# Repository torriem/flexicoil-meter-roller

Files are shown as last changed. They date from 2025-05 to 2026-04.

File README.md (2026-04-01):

A collection of CAD files pertaining to the Flexicoil 50 series and older air cart meter rollers.  An OpenSCAD library, called "Flexicoil Meter Segment.scad" creates various kinds of meter roller segments, for 3-D printing.  Currently implemented roller types are extra fine (canola), fine (wheat), coarse (fertlizer, peas), extra coarse (large peas etc), and blank, with a 1 1/8" hex hole through them.  Dimensions defining the diameter and width of the rollers, as well as printer tolerances for the hex hole, are in dimensions.scad.

dimensions.scad defines common dimensions used by all the meter roller segment types and Flexicoil Meter Segment.scad contains parametric segment creator modules.

`Extra Fine Segments.scad`, `Fine Segments.scad`, `Coarse Segments.scad`, and `Extra Coarse Segments.scad` demonstrate all of the variants of the different segment types possible.  In order to create an STL of a specific variant, comment out the other module calls in the scad file before exporting to STL.

Most objects can be printed without supports.  The bearing endcap can be printed as it renders (with the open cup up) with supports in TPU 95A, with between 25 and 50% infill.  Supports, even when made with TPU, seem to remove pretty well.  

Meter segments seem to print quite well with TPU 95A, with 5 walls and 30% infill.  The mechanical properties end up being very similar to the OEM parts.

Spacers and Bushings can be printed out of either ABS or PETG.  You will likely have to adjust the tolerances to get a good fit on the shaft and bearings.

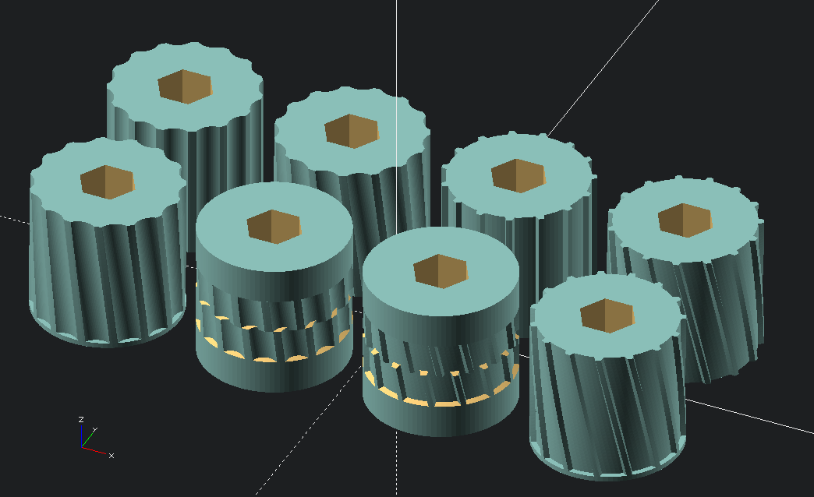
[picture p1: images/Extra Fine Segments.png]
Extra Fine Segments


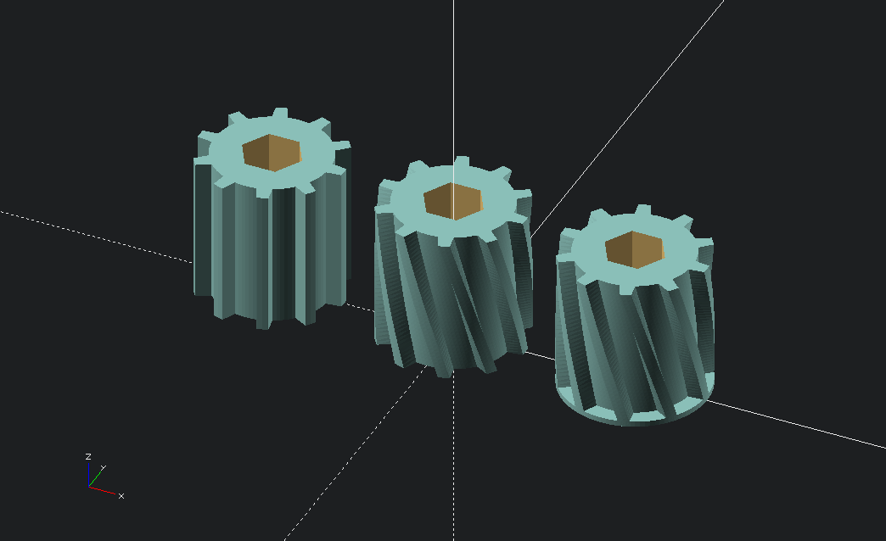
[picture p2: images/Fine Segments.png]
Fine Segments


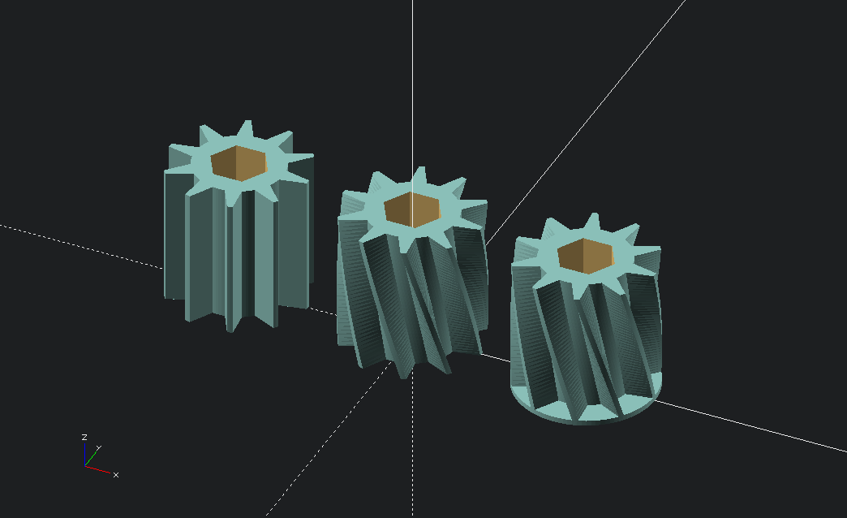
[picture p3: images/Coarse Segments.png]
Coarse Segments


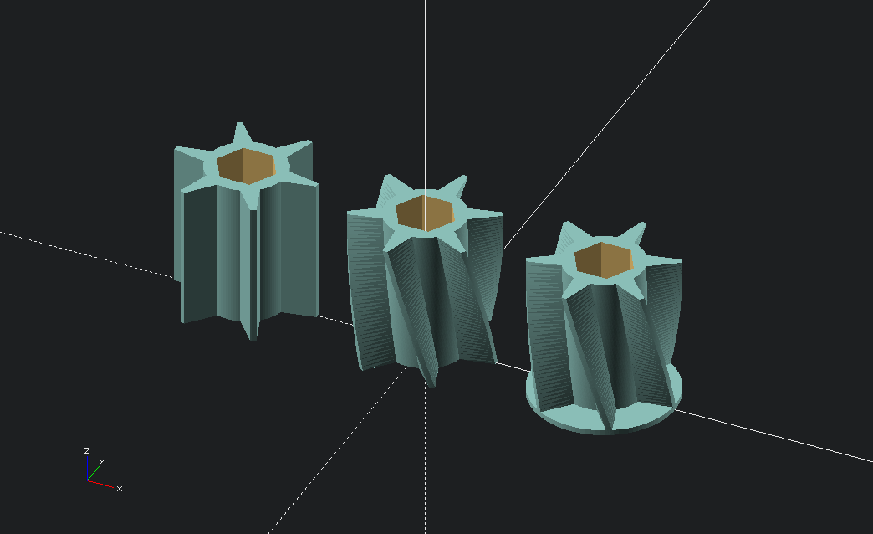
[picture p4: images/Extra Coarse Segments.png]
Extra Coarse Segments


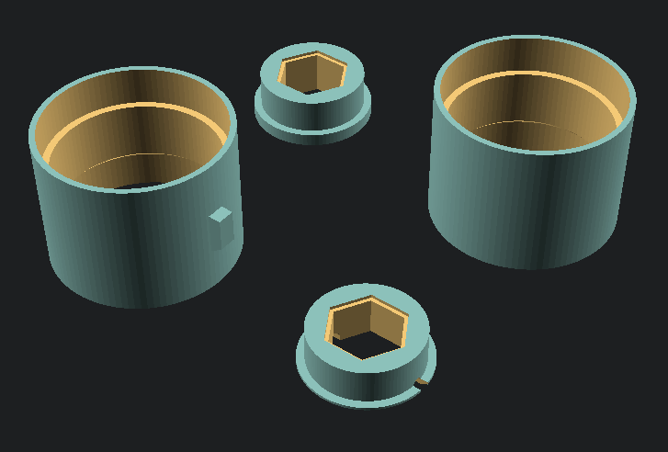
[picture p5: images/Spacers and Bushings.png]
Spacers and Bushings


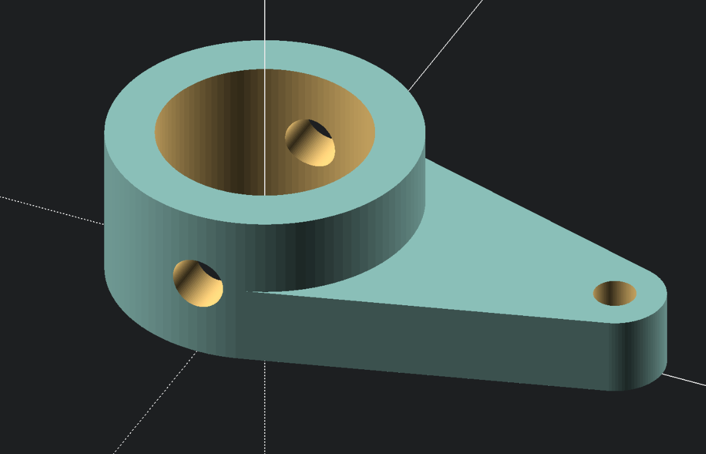
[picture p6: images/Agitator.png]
Agitator Cam


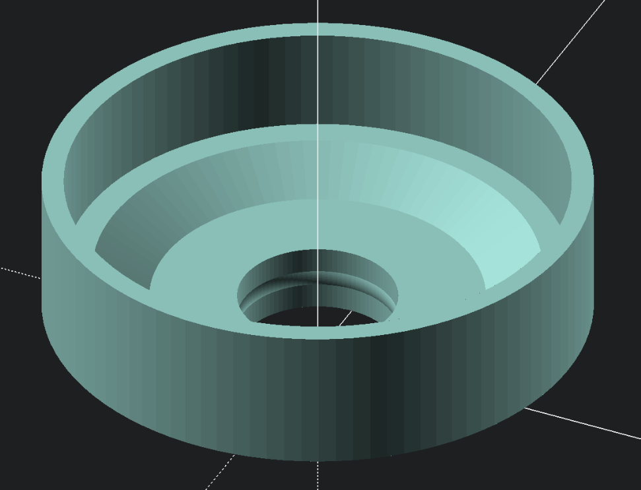
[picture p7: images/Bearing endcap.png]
Bearing endcaps


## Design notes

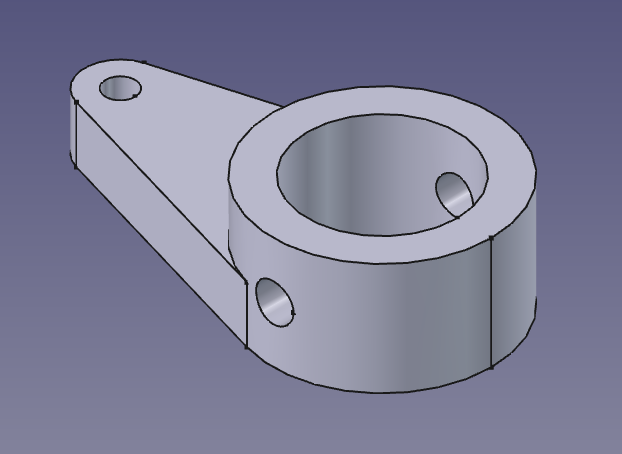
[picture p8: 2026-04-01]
FreeCAD/images/Agitator.png

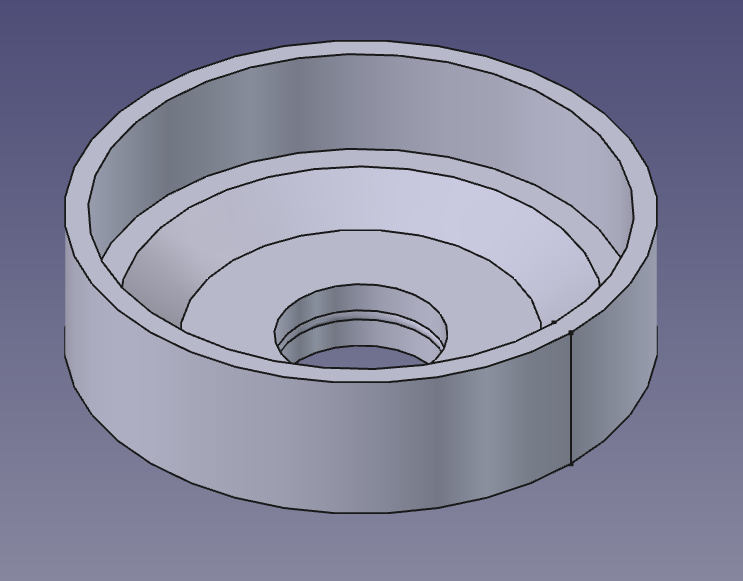
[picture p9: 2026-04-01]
FreeCAD/images/Bearing endcap.png

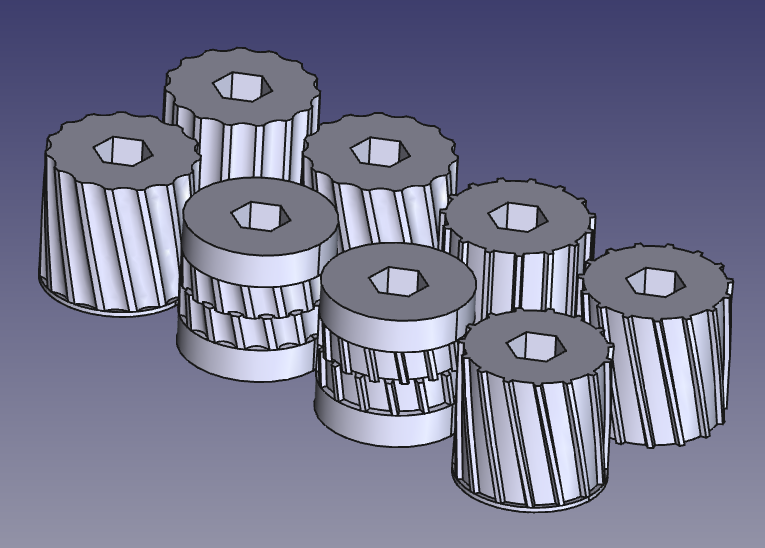
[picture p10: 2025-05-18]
FreeCAD/images/Extra Fine.png

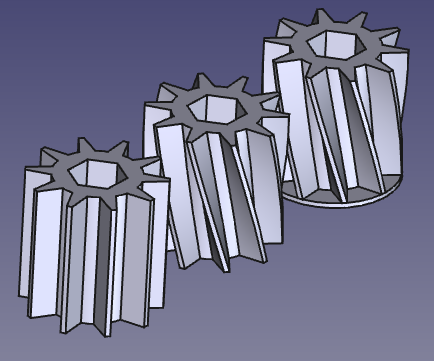
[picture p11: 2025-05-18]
FreeCAD/images/Coarse.png

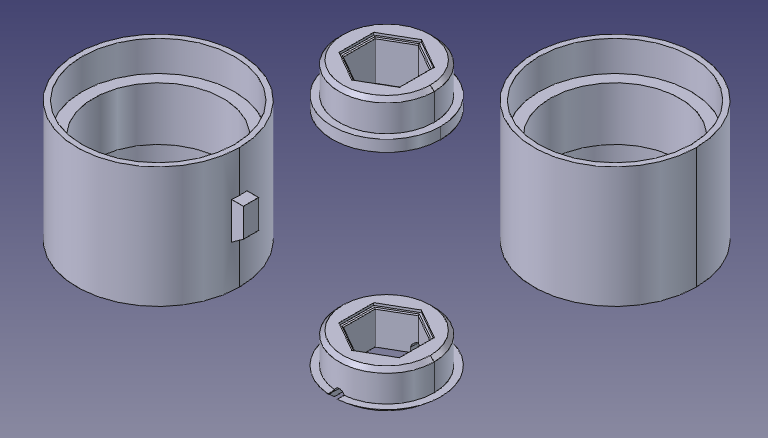
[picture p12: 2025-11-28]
FreeCAD/images/Spacers and Bushings.png

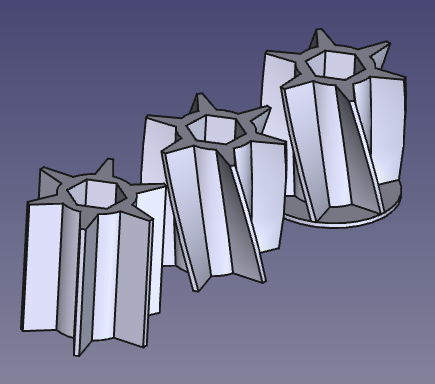
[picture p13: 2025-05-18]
FreeCAD/images/Extra Coarse.png

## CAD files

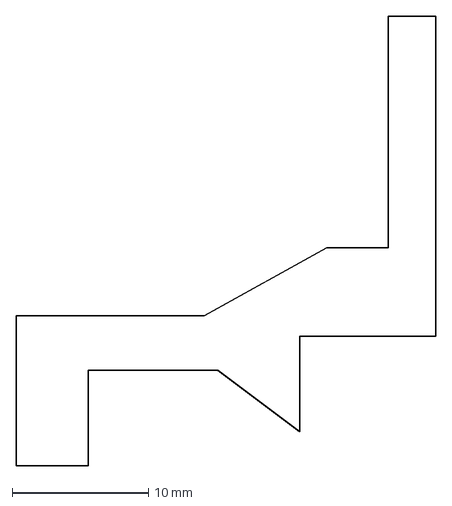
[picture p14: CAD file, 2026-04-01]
Bearing endcap-Sketch.dxf
30.8 x 33.0 mm

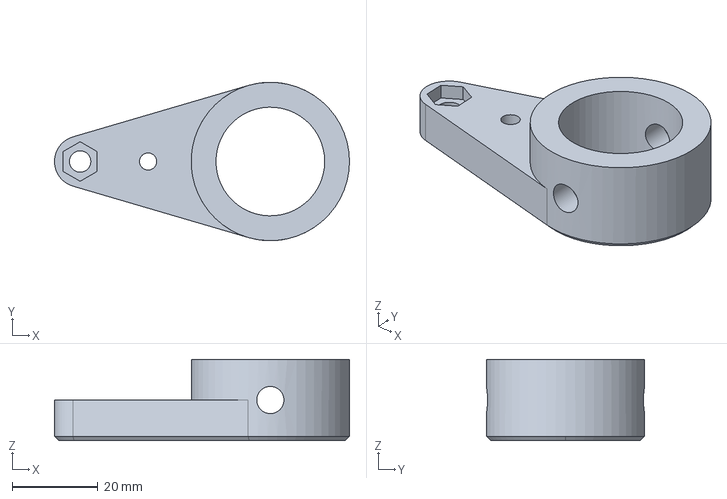
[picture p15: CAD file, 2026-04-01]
FreeCAD/Agitator cam.FCStd
68.9 x 37.0 x 19.0 mm

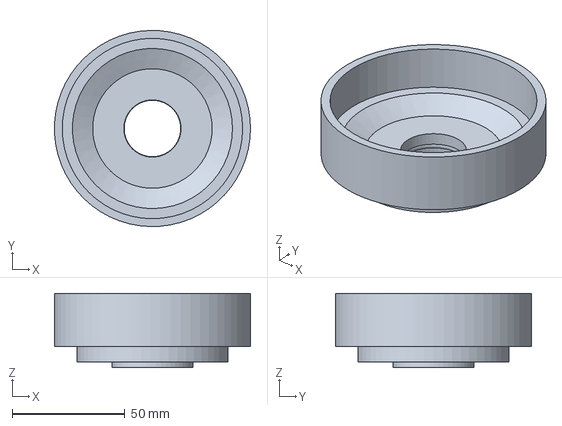
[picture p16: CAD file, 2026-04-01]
FreeCAD/Bearing endcap.FCStd
86.9 x 87.0 x 33.0 mm

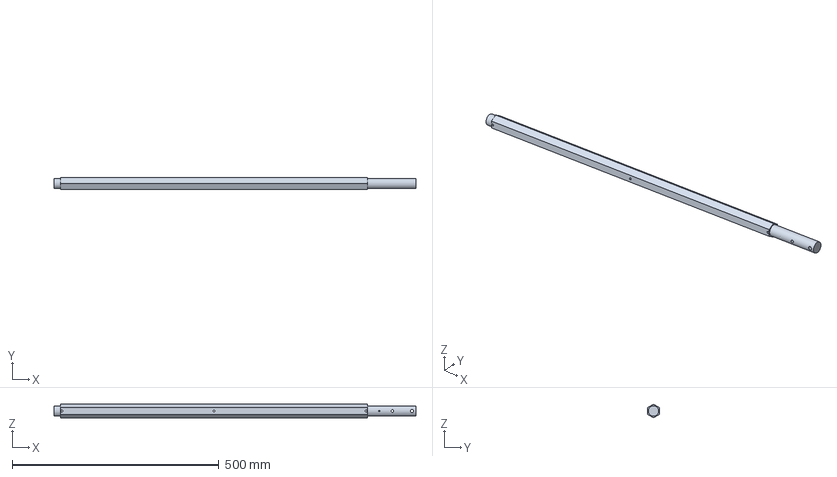
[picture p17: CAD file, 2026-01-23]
FreeCAD/Shaft.FCStd
876.3 x 28.6 x 33.0 mm

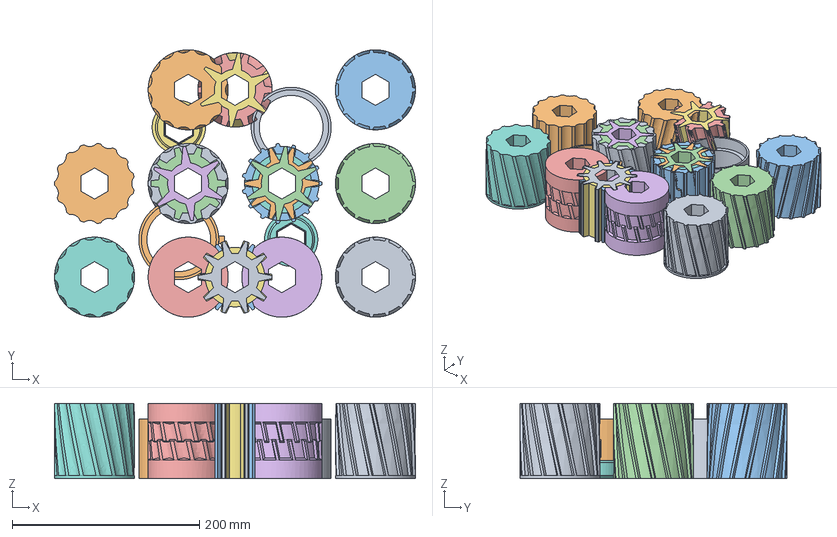
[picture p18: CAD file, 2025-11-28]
FreeCAD/Flexicoil Meter Segments.FCStd
385.5 x 285.5 x 80.2 mm
Extra Fine Spiral
Extra Fine
Extra Fine Fluted
Extra Fine Fluted Spiral
Canola Test 1
Canola Test 2
Fine
Fine Spiral
Coarse
Coarse Spiral
Extra Coarse
Extra Coarse Spiral
Fine Divider Spiral
Coarse Spiral Divider
Extra Coarse Spiral Divider
Extra Fine Spiral Divider
Extra Fine Fluted Spiral Divider
Extra Fine Right-Hand Spiral
Extra Fine Fluted Right-Hand Spiral
Fine Right-Hand Spiral
Coarse Right-Hand Spiral
Extra Coarse Right-Hand Spiral
Bearing bushing
Bearing end bushing
Spacer without nub
Spacer with nub

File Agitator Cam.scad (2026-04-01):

include <dimensions.scad>

$fn=100;

difference() {
	//basic shape
	union() {
		linear_extrude(9.525) {
			hull() {
				translate( [44.45, 0] ) {
					circle(6);
				}
				circle(18.5);
			}
		}
		cylinder( 19, 18.5, 18.5);
	}	

	//1" shaft hole
	cylinder( 19, 12.7, 12.7);

	//5mm hole with hex pocket for nut for the
	//cam bearing
	translate( [44.45, 0, 0] ) {
		union() {
			cylinder(10,2.5,2.5);
			translate([0,0,6.525]) {
				rotate([0,0,30]) {
					cylinder(3,4,4,$fn=6);
				}
			}
		}
	}

	//screw hole for attaching label
	translate( [1.125 * inches,0,0] ) {
		cylinder(10,2,2);
	}

	//0.25" hole for the roll pin
	translate([0,0,9.5]) {
		rotate([90,0,0]) {
			cylinder(50,3.175, 3.175, center=true);
		}
	}
}

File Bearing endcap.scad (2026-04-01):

include <dimensions.scad>

$fn=100;

union() {
	//basic shape, imported from a dxf designed in
	//FreeCAD
	rotate_extrude() {
		import("Bearing endcap-Sketch.dxf");
	}

	//add small sealing surface to keep dust out
	//similar to OEM part
	rotate_extrude() {
		translate([16.75, 5.5]) {
			circle(4.25);
		}
	}
}

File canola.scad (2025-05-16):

include <Flexicoil Meter Segment.scad>

flute_depth = 3; //common depth for all versions below

translate([-100,100,0])
	extra_fine(spiral=false, scallop_depth = flute_depth);
translate([100,100,0])
	extra_fine(spiral=true, scallop_depth = flute_depth);
translate([-100,-100,0])
	extra_fine_fluted(spiral=false, flute_depth = flute_depth);
translate([100,-100,0])
	extra_fine_fluted(spiral=true, flute_depth = flute_depth);
canola_experimental(flute_depth);

/* An experimental segment design for canola that uses
   flutes like the OEM fine roller, but very shallow,
   and only half width.
*/
module canola_experimental(flute_depth = extra_fine_flute_depth) {

	union() {
		segment_part(segment_width, segment_diameter_tight, 0, 25, top_chamfer = 3)
			blank(segment_width);

		translate([0,0,segment_width / 4])
			segment_part(segment_width, segment_diameter_tight, 0, 25, top_chamfer = flute_depth)
				extra_fine_fluted(segment_width, spiral=true, flute_depth=flute_depth);
				//extra_fine(segment_width, spiral=true, scallop_depth=flute_depth);
		translate([0,0,segment_width / 4 * 2])
			segment_part(segment_width, segment_diameter_tight, 75, 100, bottom_chamfer = flute_depth)
				extra_fine_fluted(segment_width, spiral=true, flute_depth=flute_depth);
				//extra_fine(segment_width, spiral=true, scallop_depth=flute_depth);
		translate([0,0,segment_width / 4 * 3])
			segment_part(segment_width, segment_diameter_tight, 75, 100, bottom_chamfer = flute_depth)
				blank(segment_width);
	}
}

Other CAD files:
Coarse Segments.scad
Extra Coarse Segments.scad
Extra Fine Segments.scad
Fine Segments.scad
Flexicoil Meter Segment.scad
demo.scad
dimensions.scad
flexicoil spacers and bushings.scad
hex tolerance test.scad
spacers demo.scad

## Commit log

2025-05-08 Added readme and demo file.
    [demo.scad]
2025-05-08 Added GPLv3 license to scad code.
    [Flexicoil Meter Segment.scad]
2025-05-08 turned off some debugging echoes
    [Flexicoil Meter Segment.scad]
2025-05-13 Increased diameter of extra fine roller to 85.5mm
    [Flexicoil Meter Segment.scad, dimensions.scad]
2025-05-13 experimental canola roller, also modeled center spacer.
    [canola.scad, spacer.scad]
2025-05-14 Added a module to return an arbitrary portion of segment, and optionally chamfer the top and bottom outer edges. Created an experimental canola segment, hoping to work better at low rates (2-3 #/ac).
    [Flexicoil Meter Segment.scad, canola.scad]
2025-05-16 minor code cleanup
    [Flexicoil Meter Segment.scad, canola.scad]
2025-05-16 default depth of flute or scallop for extra fine roller now defined in dimensions.scad
    [Flexicoil Meter Segment.scad, dimensions.scad]
2025-05-16 experimental canola roller segment now it's own module. canola.scad demos extra_fine (oem-style) and extra_fine_fluted, both spiraled and straight. Also demos the experimental canola segment.
    [canola.scad]
2025-05-16 Added a hex tolerance test object that can be printed to verify fit on the hex shaft.
    [dimensions.scad, hex tolerance test.scad]
2025-05-18 added a divider modifier module, renamed canola.scad to extrafine.scad
    [Flexicoil Meter Segment.scad, extrafine.scad]
2025-05-18 Divider can be either bigger diameter for extra fine rollers, or normal diameter for fine, coarse, and extra coarse diameters.
    [Flexicoil Meter Segment.scad, extrafine.scad]
2025-05-18 Added scad files to show variants of each type of roller. Extra Fine, Fine, Coarse, and Extra Coarse.
    [Coarse Segments.scad, Extra Coarse Segments.scad, Extra Fine Segments.scad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]
2025-05-18 Removed redundant code from main scad file because we now use a modifier module called add_divider() to render dividers. This removes a lot of redundant code. Also reorganized some files.
    [Flexicoil Meter Segment.scad]
2025-05-18 freecad versions
    [Shaft.FCStd]
2025-05-24 By specifying a negative twist number can spiral in the opposite direction. Added demos to show this.
    [Coarse Segments.scad, Extra Coarse Segments.scad, Extra Fine Segments.scad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]
2025-06-01 Added parameters to segment_part(), bottom_chamfer(), and top_chamfer() to set the desired bevel angle for the chamfer cut. Also changed the half roller demonstrations in Extra Fine Segments.scad to 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
    [Extra Fine Segments.scad, Flexicoil Meter Segment.scad, hex tolerance test.scad]
2025-11-28 Added standard bearing bushings and spacers to scad
    [Flexicoil Meter Segment.scad, dimensions.scad, spacer.scad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]
2025-11-28 Added standard bearing bushings and spacers to freecad parametric model
    [Flexicoil Meter Segments.FCStd]
2025-11-28 demo for spacers to show all of them.
    [spacers demo.scad]
2025-11-28 Update README and pictures of spacers and bushings.
2025-12-06 Figured out tolerances for petg and abs, added inner spacer for center spacer assembly.
    [Flexicoil Meter Segment.scad, dimensions.scad, flexicoil spacers and bushings.scad]
2025-12-06 chamferred underside of pinned bushing
    [Flexicoil Meter Segment.scad]
2026-01-23 re-add FreeCAD files with zip-store filter for more efficient git deltas.
    [Shaft.FCStd]
2026-04-01 Implemented the agitator cam and bearing end cap in FreeCAD.
    [Agitator cam.FCStd, Bearing endcap.FCStd]
2026-04-01 Implemented agitator cam in openscad. Updated images. Also changed the small end of the agitator to 6mm diameter.
    [Agitator Cam.scad, Agitator cam.FCStd]
2026-04-01 Fixed variable names in dimensions.scad. Added bearing encap models.
    [Agitator Cam.scad, Bearing endcap-Sketch.dxf, Bearing endcap.scad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]
2026-04-01 hex pocket for screw was on the wrong side. Also added screw hole for label to agitator cam.
    [Agitator Cam.scad, Agitator cam.FCStd]
